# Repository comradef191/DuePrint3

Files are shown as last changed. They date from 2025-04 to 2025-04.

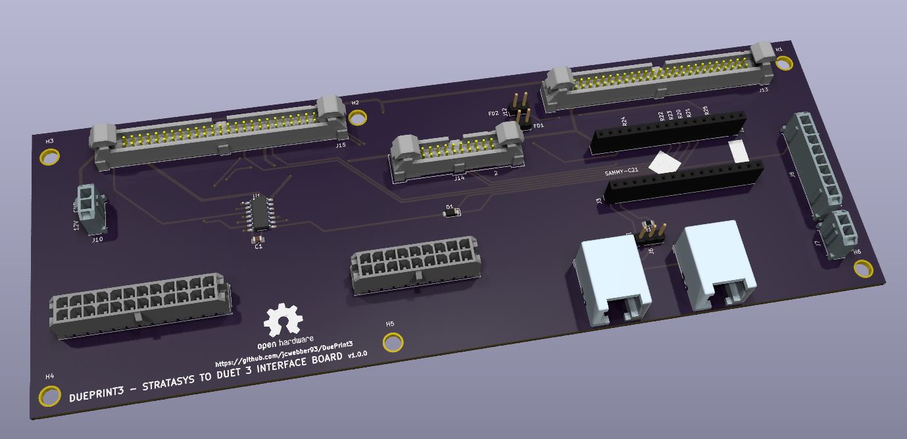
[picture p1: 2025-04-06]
DuePrint3 v1.0.0.JPG

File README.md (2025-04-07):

# DuePrint3
Duet 3 to Stratasys PDB Interface Board. Used to convert a Stratasys Prodigy series printer (Dimension, uPrint, Fortus 250) to use a modern control board & firmware. This conversion is fully reversable (assuming the printer functions to begin with). Many thanks to AJ Quick and Archeantus (Jeremy) for their past efforts in detailing the electronics of the Dimension/uPrint machines, as well as sharing details on their Duet 2 WiFi conversions.
* https://wiki.cnc.xyz/Stratasys_uPrint_Retrofit
* https://forum.duet3d.com/topic/12647/another-stratasys-uprint-retrofit

[Additional details for this project on the Duet3D forums.](https://forum.duet3d.com/topic/37434/dueprint-with-a-duet-3-6hc-stratasys-dimension-conversion)

DuetPrint3 Block Diagram

sIMG_3466

DuePrint3 v1 0 0

At present, the implementation focuses on the Dimension 1200es printers (the implementations linked above focus on the uPrint series, which is quite similar. The electronics are laid out a touch differently, meaning the layout of the new hardware must change, as well where the stepper motor wiring taps in to the existing harness). The Duet 3 Mainboard 6HC, as well as the Sammy-C21 module (natively running RepRapFirmware) interface with 19 inputs, and 9 outputs.
### Inputs
|Input|Description|GCode|Note|
|---|---|---|---|
|6HC IO_7 io7.in|PRINT HEAD TEMP ALARM|`M950 J9 C"!io7.in" ; Print Head Temp Alarm`|Feature not yet implemented|
|6HC IO_2 io2.in|PRINT BED TOUCH PR LIM SW|`M558 P5 H5 F1200:200 T18000 A3 C"!io2.in" ; Z probe`|Used in bed probing|
|6HC IO_6 io6.in|Z-AXIS EOT|`M574 Z2 S1 P"!io6.in"  ; assign Z EOT to x endstop on high side`|Used as part of homing (find max Z)|
|6HC IO_8 io8.in|CHAMBER TEMP ALARM|`M950 J10 C"!io8.in" ; Chamber Temp Alarm`|Feature not yet implemented|
|6HC IO_4 io4.in|Y-AXIS EOT|`M950 J6 C"!io4.in" ; Y-axis EOT`|Used in macro to measure max Y|
|6HC IO_3 io3.in|X-AXIS EOT|`M950 J5 C"!io3.in" ; X-axis EOT`|Used in macro to measure max X|
|6HC IO_0 io0.in|X-AXIS HOME SW|`M574 X1 S1 P"!io0.in" ; X home limit (low side)`|Used in homing|
|6HC IO_1 io1.in|Y-AXIS HOME SW|`M574 Y1 S1 P"!io1.in" ; Y home limit (low side)`|Used in homing|
|6HC IO_5 io5.in|Z-AXIS HOME SW|`M950 J7 C"!io5.in" ; Z-axis Home`|I/O works, Feature not yet implemented|
|SAMMY-C21 PB08|Filament Detection 2|Not Implemented|Feature not yet implemented|
|SAMMY-C21 PA04|Gecko Error|`M950 J0 C"124.pa04" ; Gecko Error In`|Was used to detect an error on Geckodrive G320x. No longer used|
|SAMMY-C21 PA05|HEAD THERMOSTAT STATUS|`M950 J1 C"124.pa05" ;Head Thermostat Status`|Feature not yet implemented|
|SAMMY-C21 PA06|DOOR SWITCH|`M950 J2 C"124.pa06" ; Door`|I/O works, Feature not yet implemented|
|SAMMY-C21 PA07|SUPPORT TOGGLE SW|`M950 J3 C"124.pa07" ; Support Toggle`|Sense Support toolchange|
|SAMMY-C21 PA12|Filament Detection 1|Not Implemented|Feature not yet implemented|
|SAMMY-C21 PA19|MODEL TOGGLE SW|`M950 J4 C"124.pa19" ; Model Toggle`|Sense Model toolchange|
|6HC TEMP_0 VSSA & temp0|CHAMBER THERM|`M308 S0 A"Chamber Test" P"temp0" Y"linear-analog" F0 B-42 C113`||
|6HC TEMP_1 VSSA & temp1|MODEL THERM|`M308 S1 A"Model Test" P"temp1" Y"linear-analog" F0 B12.5 C328`||
|6HC TEMP_2 VSSA & temp2|SUPPORT THERM|`M308 S2 A"Support Test" P"temp2" Y"linear-analog" F0 B12.5 C328`||

### Outputs
|Output|Description|GCode|Note|
|---|---|---|---|
|6HC OUT_8 V_OUTLC8 & out8|EXTRUDER MODEL HEATER ENA|`M950 H1 C"!out8" T1 ; Model, sensor 1`|
|6HC OUT_9 V_OUTLC9 & out9|SUPPORT HEATER ENA|`M950 H2 C"!out9" T2 ; Support, sensor 2`|
|6HC IO_2 io2.out|LED LIGHTS ENA|`M950 P4 C""io2.out"" ; LED Lights - M42 P4 S1 ; lights on`|
|6HC IO_6 io6.out|DOOR SOLENOID ENA|`M950 P3 C""io6.out"" ; Door Solenoid - M42 P3 S0 ; unlocked`|
|6HC OUT_7 V_OUTLC7 & out7|CHAMBER HEATER ENA|`M950 H0 C"!out7" T0 ; Chamber, sensor 0`||
|6HC OUT_6 V_OUTLC6 & out6|PRINT BED TOUCH PR ENA|`M950 P2 C""!out6"" ; Touch Power Enable` - `M42 P2 S0`|Unsure on purpose? Doesn't seem to function at all/as expected|
|6HC IO_0 io0.out|GECKO RESET|`M950 P5 C""io0.out"" ; Gecko Reset` - `M42 P5 S0`|Was used to reset an error on Geckodrive G320x. No longer used|
|6HC OUT_5 V_OUTLC5 & out5|MOTOR ENA|`M950 P1 C""!out5"" ; Extruder Motor` - `M42 P1 S0 ; motor off`|
|6HC OUT_4 V_OUTLC4 & out4|BLOWER ENA|`M950 P0 C""!out4"" ; Head Blower Fan` - `M42 P0 S0 ; enable blower`|

The 6HC directly drives the X, Y, and Z stepper motors (vs. controlling them through the Stratasys PDB). The 6HC, unlike the Duet2 (and Duex boards) does not natively have STEP/DIR pins used to emit step and direction pulses. Instead, a Sammy-C21 ([running RepRapFirmware](https://docs.duet3d.com/Duet3D_hardware/Duet_3_family/Using_the_Sammy-C21_development_board_with_Duet_3)) is used to emit step and direction pulses to a STM32 Nucelo-64, which in turn is running [SimpleDCMotor](https://github.com/simplefoc/Arduino-FOC-dcmotor) to control the extruder's closed loop DC motor. Note that this design was initially setup to use a Geckodrive G320x, however early into commissioning, I burnt up a few series resistors and a 74AC14 on the PDB. The Nucleo-64 with SimpleDCMotor is a much better solution, with a significantly lower cost.

## Materials
[A detailed BOM can be found here](https://github.com/jcwebber93/DuePrint3/blob/main/DuePrint3%20BOM.xlsx), with the approximate cost being ~$500 (60% of this is Duet3D 6HC and Sammy-C21).

## Interface Board Design
[The KidCad project for the DuePrint3 board can be found here](https://github.com/jcwebber93/DuePrint3/tree/main/DuePrint3%20KiCad%20Project)

## Wiring
[A detailed wire list can be found here.](https://github.com/jcwebber93/DuePrint3/blob/main/DuePrint3%20Wire%20List.xlsx) Connectors & crimps for the Duet 3 6HC are supplied with the board, but are JST VH (stepper motors) and Molex KK / Wurth WR-WTB (Wurth connectors/contacts are supplied with Duet Boards). Interface board uses Molex Micro-3.0 series connectors & crimps, whereas the connectors for the PBD ribbon cables are Samtec EHT headers.

> [!WARNING]
> Do not connect connectors `P13`, `P20`, and `P26` (Model heater, support heater, chamber heater) to the 6HC until after the model, support, and chamber thermocouple functionality has been validated

## Sammy-C21 Prep
If using a Sammy-C21 purchased with the preloaded Duet3D bootloader, no special programming is needed. J100 needs to be unbridged, as 5V is supplied to pins 15 and 32 (V33, for 5V logic, and VCC).



## Interface Board Prep
If the Interface Board (w/Sammy-C21) is the only CAN-FD device, aside from the Duet 3 6HC, place a 2-socket jumper here to enable the CAN-FD termination resistor.



J4 connects to the 6HC. J5 (marking suspiciously missing on silkscreen) can be used with additional expansion boards (such as a Duet 3 SZP on the print head, could be used as an accelerometer or for bed scanning), provided the CAN-FD bus is terminated on the additional board.

## RepRapFirmware Prep
At present, the 6HC and Sammy-C21 are running 3.6.0-rc.1 (April 2025). [Configuration files are located here](https://github.com/jcwebber93/DuePrint3/tree/main/Duet%203%20Configuration/System%20Directory), and [Macros are located here.](https://github.com/jcwebber93/DuePrint3/tree/main/Duet%203%20Configuration/Macros%20Directory)

> [!WARNING]
> Do not connect connectors `P13`, `P20`, and `P26` (Model heater, support heater, chamber heater) to the 6HC until after the model, support, and chamber thermocouple functionality has been validated (a spare K-type thermocouple can be used to validate the linear-analog values in the `M308` commands - ice water and boiling water (for the chamber), boiling water for the extruders)

## SimpleDCMotor / Nucleo-64
[Sketch located here](https://github.com/jcwebber93/DuePrint3/tree/main). Prep your build enviornment [per the SimpleFOC documentation.](https://docs.simplefoc.com/) I used Ardiono IDE, and [added boards via](https://github.com/stm32duino/Arduino_Core_STM32/wiki/Getting-Started). I bench programmed the Nucleo-64, then prepped it for install in the Stratasys by janging jumper JP5 to set power via E5V instead of U5V (USB).

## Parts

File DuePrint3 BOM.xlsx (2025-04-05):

 |  |  |  |  | $471.09
Item | Part Number | Description | Quantity | REF | Price | EXT Price | Note | Link
1 |  | Duet 3 Mainboard 6HC | 1 |  | $269.99 | $269.99 |  | https://www.filastruder.com/collections/duet3d/products/duet-3-mainboard-6hc
2 | C45_SC21-D3D | SAMMY-C21 Module | 1 |  | $34.99 | $34.99 | Likely need to source 16pin headers | https://www.filastruder.com/products/sammy-c21-v1-0-duet3d-module
3 | NUCLEO-L476RG | STM32 Nucleo-64, L476RG | 1 |  | $23.99 | $23.99 | Need USB Mini B cable for programming | https://www.amazon.com/dp/B01IO3N646
4 |  | DuePrint3 v1.0.0 PCB | 1 |  | $40.60 | $40.60
5 | LRS-75-48 | Power Suppy, AC/DC, 48V 75W | 1 |  | $15.60 | $15.60 | AC is spliced in from the printer's power inlet, meaning right now the Duet's power cannot be controlled from front on/off switch (though front on/off switch functionality is also not fully present on PCB) | https://www.digikey.com/en/products/detail/mean-well-usa-inc/LRS-75-48/7705054
6 | 430452412 | Conn, Header, 24 pos, Micro-Fit 3.0 | 1 | J1 | $3.51 | $3.51 |  | https://www.digikey.com/en/products/detail/molex/0430452412/531416
7 | 430451812 | Conn, Header, 18 pos, Micro-Fit 3.0 | 1 | J9 | $2.48 | $2.48 |  | https://www.digikey.com/en/products/detail/molex/0430451812/531413
8 | EHT-120-01-S-D | Conn, Header, 40 pos, EHT | 2 | J13,J15 | $13.46 | $26.92 |  | https://www.digikey.com/en/products/detail/samtec-inc/EHT-120-01-S-D/1106698
9 | EHT-110-01-S-D | Conn, Header, 20 pos, EHT | 1 | J14 | $6.54 | $6.54 |  | https://www.digikey.com/en/products/detail/samtec-inc/EHT-110-01-S-D/1106695
10 | PPPC161LFBN-RC | Conn, Header, 16 pos | 2 | J2,J3 | $0.93 | $1.86 |  | https://www.digikey.com/en/products/detail/sullins-connector-solutions/PPPC161LFBN-RC/810188
11 | 54601-906002WPLF | Conn, 6p4c R/A | 2 | J4,J5 | $0.20 | $0.40 |  | https://www.digikey.com/en/products/detail/amphenol-cs-fci/54601-906002WPLF/4242890
12 | 436500215 | Conn, Header, 2 pos, MicroFit- 3.0 | 2 | J7,J10 | $0.89 | $1.78 |  | https://www.digikey.com/en/products/detail/molex/0436500215/283461
13 | M20-9990245 | Conn, Header, 2 pos | 2 | J11,J12 | $0.12 | $0.24 | Can buy larger and cut down | https://www.digikey.com/en/products/detail/harwin-inc/M20-9990245/3728225
14 | M20-9990345 | Conn, Header, 3 pos | 1 | J6 | $0.15 | $0.15 | Can buy larger and cut down | https://www.digikey.com/en/products/detail/harwin-inc/M20-9990345/3728227
15 | 436500815 | Conn, Header, 8 pos, Micro-Fit 3.0 | 1 | J8 | $1.00 | $1.00 |  | https://www.digikey.com/en/products/detail/molex/0436500815/531388
16 | CL21B104KCFSFNE | 0.1 uF Cap, 0805 | 1 | C1 | $0.10 | $0.10 |  | https://www.digikey.com/en/products/detail/samsung-electro-mechanics/cl21b104kcfsfne/3888581
17 | CRCW080531K6FKEA | 31.6K Res, 0805 | 6 | R7,R9,R11,R13,R15,R18 | $0.10 | $0.60 |  | https://www.digikey.com/en/products/detail/vishay-dale/CRCW080531K6FKEA/1175806
18 | CRCW08053K74FKEA | 3740 Res, 0805 | 6 | R8,R10,R12,R14,R16,R19 | $0.10 | $0.60 |  | https://www.digikey.com/en/products/detail/vishay-dale/crcw08053k74fkea/1175701
19 | CRCW080510K0FKEA | 10K Res, 0805 | 6 | R20,R21,R22,R23,R24,R25 | $0.10 | $0.60 |  | https://www.digikey.com/en/products/detail/vishay-dale/crcw080510k0fkea/1175751
20 | CRCW08052K00FKEA | 2K Res, 0805 | 3 | R1,R3,R4 | $0.10 | $0.30 |  | https://www.digikey.com/en/products/detail/vishay-dale/CRCW08052K00FKEA/1175669
21 | CRCW08051K00FKEA | 1K Res, 0805 | 3 | R2,R5,R6 | $0.10 | $0.30 |  | https://www.digikey.com/en/products/detail/vishay-dale/CRCW08051K00FKEA/1175637
22 | CRCW08051K00FKEA | 120 Res, 0805 | 1 | R17 | $0.10 | $0.10 |  | https://www.digikey.com/en/products/detail/vishay-dale/CRCW08051K00FKEA/1175637
23 | SS1FH10-M3/H | Schottky Diode, 100V 1A, DO-219AB | 1 | D1 | $0.32 | $0.32 |  | https://www.digikey.com/en/products/detail/vishay-general-semiconductor-diodes-division/SS1FH10-M3-H/6012246
24 | SN74AHCT125DR | SN74AHCT125DR, 14-SOIC | 1 | U1 | $0.23 | $0.23 |  | https://www.digikey.com/en/products/detail/texas-instruments/SN74AHCT125DR/376412
25 | 39012086 | Conn, Plug, 8 pos, Mini-Fit Jr | 1 | P2 | $0.66 | $0.66 |  | https://www.digikey.com/en/products/detail/molex/0039012086/930285
26 | 39012205 | Conn, Rcpt, 20 pos, Mini-Fit Jr | 1 | P3 | $1.48 | $1.48 |  | https://www.digikey.com/en/products/detail/molex/0039012205/930279
27 | 39012206 | Conn, Plug, 20 pos, Mini-Fit Jr | 1 | P1 | $1.20 | $1.20 |  | https://www.digikey.com/en/products/detail/molex/0039012206/4693014
28 | 39000041 | Pin, 18-24 AWG, Mini-Fit Jr | 10 |  | $0.15 | $1.50 | Don't use these, as they're designed for very large jackets. Recommend 39000049 instead | https://www.digikey.com/en/products/detail/molex/0039000041/61445
29 | 39000039 | Socket, 18-24 AWG, Mini-Fit Jr | 6 |  | $0.16 | $0.96 | Don't use these, as they're designed for very large jackets. Recommend 39000047 instead | https://www.digikey.com/en/products/detail/molex/0039000039/61448
30 | 430300007 | Socket, 20-24 AWG, Micro-Fit 3.0 | 43 |  | $0.18 | $7.74 |  | https://www.digikey.com/en/products/detail/molex/0430300007/252479
31 | 430252400 | Conn, Rcpt, 24 pos, Micro-Fit 3.0 | 1 | P8 | $1.34 | $1.34 |  | https://www.digikey.com/en/products/detail/molex/0430252400/531410
32 | 430251800 | Conn, Rcpt, 18 pos, Micro-Fit 3.0 | 1 | P9 | $1.07 | $1.07 |  | https://www.digikey.com/en/products/detail/molex/0430251800/531407
33 | 436450800 | Conn, Rcpt, 8 pos, Micro-Fit 3.0 | 1 | P10 | $0.35 | $0.35 |  | https://www.digikey.com/en/products/detail/molex/0436450800/531322
34 | VHR-4N | Conn, Rcpt, 4 pos, JST VH | 3 | P4,P5,P6 | $0.12 | $0.36 | Included in 6HC purchase | https://www.digikey.com/en/products/detail/jst-sales-america-inc/VHR-4N/608626
35 | SVH-21T-P1.1 | Socket, 18-22 AWG, JST VH | 12 |  | $0.12 | $1.44 | Included in 6HC purchase | https://www.mouser.com/ProductDetail/JST-Commercial/SVH-21T-P11?qs=QpmGXVUTftHffPDBVqr85w%3D%3D
36 | 61900511621 | Conn, Rcpt, 5 pos, WR-WTB | 9 | P12,P14,P15,P19,P21,P22,P23,P24,P25 | $0.17 | $1.53 | Included in 6HC purchase | https://www.digikey.com/en/products/detail/w%C3%BCrth-elektronik/61900511621/2508639
37 | 61900211621 | Conn, Rcpt, 2 pos, WR-WTB | 6 | P13,P16,P17,P18,P20,P26 | $0.13 | $0.78 | Included in 6HC purchase | https://www.digikey.com/en/products/detail/w%C3%BCrth-elektronik/61900211621/2508636
38 | 61900411621 | Conn, Rcpt, 4 pos, WR-WTB | 3 | P27,P28,P29 | $0.17 | $0.51 | Included in 6HC purchase | https://www.digikey.com/en/products/detail/w%C3%BCrth-elektronik/61900411621/2508638
39 | 61900113722DEC | Socket, 22-28 AWG, WR-WTB | 32 |  | $0.15 | $4.80 | Included in 6HC purchase | https://www.digikey.com/en/products/detail/w%C3%BCrth-elektronik/61900113722DEC/2508640
40 | QPC02SXGN-RC | Jumper, Shorting | 2 |  | $0.10 | $0.20 | For CAN-FD termination, or later filament detector connection | https://www.digikey.com/en/products/detail/sullins-connector-solutions/QPC02SXGN-RC/2618262
41 |  | CAN-FD Cable, 1m | 1 |  | $4.99 | $4.99 |  | https://www.filastruder.com/collections/duet3d/products/duet-can-fd-cable?variant=39510523281479
42 |  | 120pcs 200mm Dupont Jumpers | 1 |  | $6.98 | $6.98 | As required | https://www.amazon.com/dp/B01EV70C78
43 |  | 22 AWG Wire |  |  |  | $0.00 | As required/desired. Smaller gauges likely would be acceptable for most connections excluding motor wires | https://www.remingtonindustries.com/hook-up-wire/hook-up-wire-22-awg-stranded-solid-kit-2-color-sets-2-spool-sizes-available/
44 |  | RJ11 connectors |  |  |  | $0.00 | In case custom length/custom purpose CAN-FD cables are desired

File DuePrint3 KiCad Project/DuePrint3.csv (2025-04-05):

Reference | Value | Datasheet | Footprint | Qty | DNP
C1 | 0.1 µF | https://www.digikey.com/en/products/detail/samsung-electro-mechanics/cl21b104kcfsfne/3888581 | Capacitor_SMD:C_0805_2012Metric_Pad1.18x1.45mm_HandSolder | 1
D1 | 100v 1a | https://www.digikey.com/en/products/detail/vishay-general-semiconductor-diodes-division/SS1FH10-M3-H/6012246 | Diode_SMD:D_SMF | 1
J1 | 430452412 | https://www.digikey.com/en/products/detail/molex/0430452412/531416?s=N4IgTCBcDaICwGYAMcCsBaMcCMEC6AvkA | Connector_Molex:Molex_Micro-Fit_3.0_43045-2412_2x12_P3.00mm_Vertical | 1
J2,J3 | PPPC161LFBN-RC | https://www.digikey.com/en/products/detail/sullins-connector-solutions/PPPC161LFBN-RC/810188 | Connector_PinSocket_2.54mm:PinSocket_1x16_P2.54mm_Vertical | 2
J4,J5 | 6P2C | https://www.digikey.com/en/products/detail/amphenol-cs-fci/54601-906002WPLF/4242890 | Connector_RJ:RJ12_Amphenol_54601-x06_Horizontal | 2
J6 | Conn_01x03_Pin | ~ | Connector_PinHeader_2.54mm:PinHeader_1x03_P2.54mm_Vertical | 1
J7,J10 | 436500215 | https://www.digikey.com/en/products/detail/molex/0436500215/283461?s=N4IgTCBcDaICwGYBsBWADAWjWAjCkAugL5A | Connector_Molex:Molex_Micro-Fit_3.0_43650-0215_1x02_P3.00mm_Vertical | 2
J8 | 436500815 | https://www.digikey.com/en/products/detail/molex/0436500815/531388 | Connector_Molex:Molex_Micro-Fit_3.0_43650-0815_1x08_P3.00mm_Vertical | 1
J9 | 430451812 | https://www.digikey.com/en/products/detail/molex/0430451812/531413 | Connector_Molex:Molex_Micro-Fit_3.0_43045-1812_2x09_P3.00mm_Vertical | 1
J11,J12 | Conn_01x02_Pin | ~ | Connector_PinHeader_2.54mm:PinHeader_1x02_P2.54mm_Vertical | 2
J13,J15 | EHT-125-01-S-D | https://www.digikey.com/en/products/detail/samtec-inc/EHT-120-01-S-D/1106698 | EHT-125-01-S-D:SAMTEC_EHT-125-01-S-D | 2
J14 | EHT-110-01-S-D | https://www.digikey.com/en/products/detail/samtec-inc/EHT-110-01-S-D/1106695 | EHT-110-01-XX-D:EHT-110-01-XX-D | 1
R1,R3,R4 | 2K | https://www.digikey.com/en/products/detail/vishay-dale/CRCW08052K00FKEA/1175669 | Resistor_SMD:R_0805_2012Metric_Pad1.20x1.40mm_HandSolder | 3
R2,R5,R6 | 1K | https://www.digikey.com/en/products/detail/vishay-dale/CRCW08051K00FKEA/1175637 | Resistor_SMD:R_0805_2012Metric_Pad1.20x1.40mm_HandSolder | 3
R7,R9,R11,R13,R15,R18 | 31.6K | https://www.digikey.com/en/products/detail/vishay-dale/CRCW080531K6FKEA/1175806 | Resistor_SMD:R_0805_2012Metric_Pad1.20x1.40mm_HandSolder | 6
R8,R10,R12,R14,R16,R19 | 3740 | https://www.digikey.com/en/products/detail/vishay-dale/crcw08053k74fkea/1175701 | Resistor_SMD:R_0805_2012Metric_Pad1.20x1.40mm_HandSolder | 6
R17 | 120 | https://www.digikey.com/en/products/detail/vishay-dale/CRCW08051K00FKEA/1175637 | Resistor_SMD:R_0805_2012Metric_Pad1.20x1.40mm_HandSolder | 1
R20,R21,R22,R23,R24,R25 | 10k | https://www.digikey.com/en/products/detail/vishay-dale/crcw080510k0fkea/1175751 | Resistor_SMD:R_0805_2012Metric_Pad1.20x1.40mm_HandSolder | 6
U1 | SN74AHCT125DR | https://www.digikey.com/en/products/detail/texas-instruments/SN74AHCT125DR/376412 | Stratasys Adapter:SOIC127P600X175-14N | 1

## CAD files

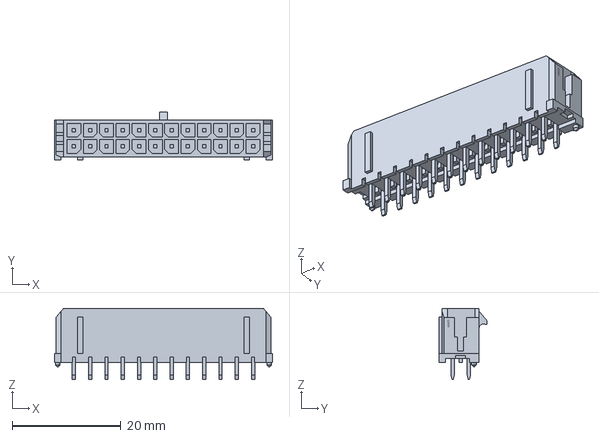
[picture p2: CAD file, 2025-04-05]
DuePrint3 KiCad Project/Components/MF3-2x12-430452427.stp
40.1 x 8.77 x 13.1 mm

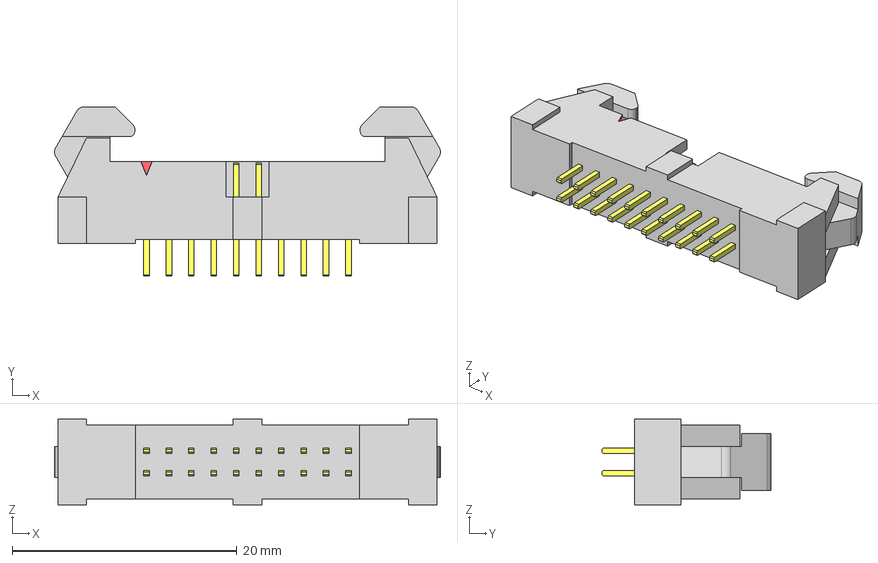
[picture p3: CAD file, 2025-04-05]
DuePrint3 KiCad Project/Components/EHT-110-01-XX-D.step
34.4 x 15.1 x 7.62 mm
C-95-01-10-D-
EHT-First_Position_Indicator
EHT-110-01-D_header

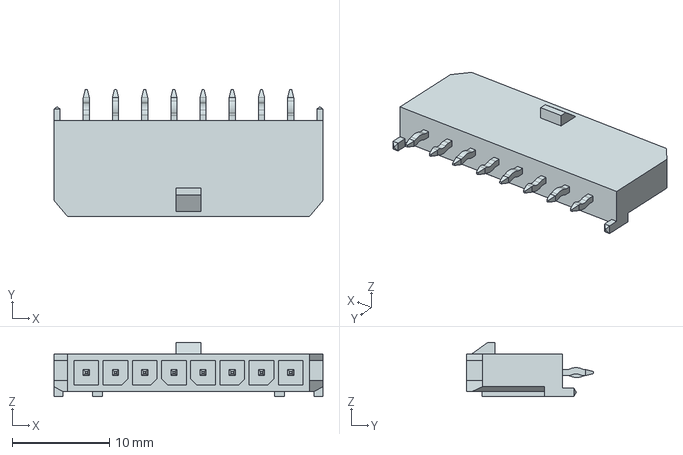
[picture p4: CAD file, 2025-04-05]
DuePrint3 KiCad Project/Components/MF3-1x8-436500815.stp
27.6 x 13.1 x 5.57 mm

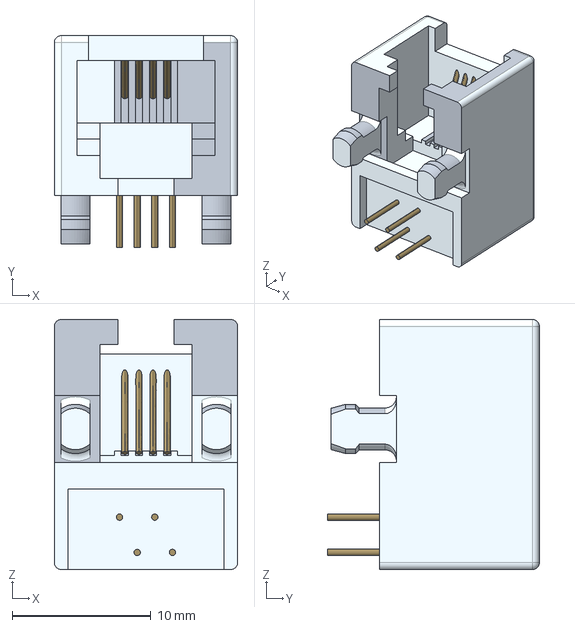
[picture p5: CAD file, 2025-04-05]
DuePrint3 KiCad Project/Components/RJ11-54601.igs
13.2 x 15.2 x 18.0 mm

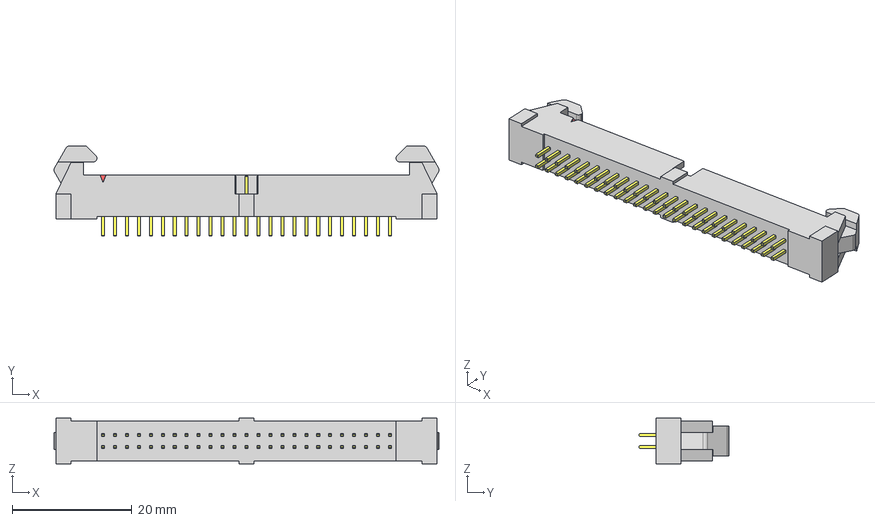
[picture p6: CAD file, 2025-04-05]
DuePrint3 KiCad Project/Components/EHT-125-01-S-D.step
64.4 x 15.1 x 7.62 mm
C-95-01-25-D-
EHT-First_Position_Indicator
EHT-125-01-D_header

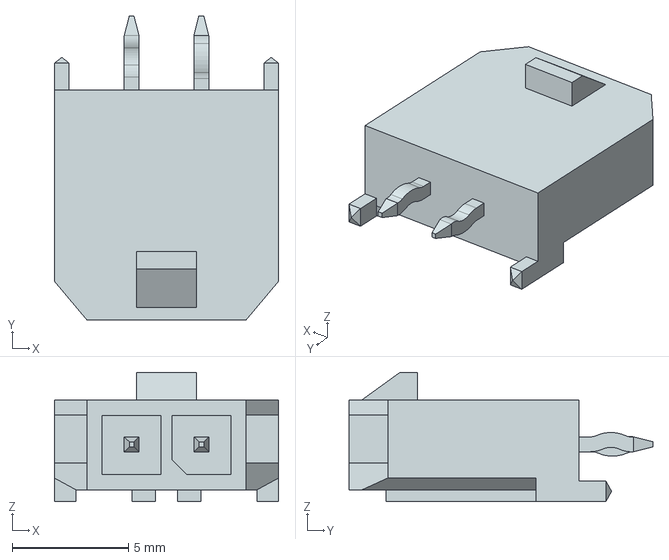
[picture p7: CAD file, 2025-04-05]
DuePrint3 KiCad Project/Components/MF3-1x2-436500215.stp
9.65 x 13.1 x 5.57 mm

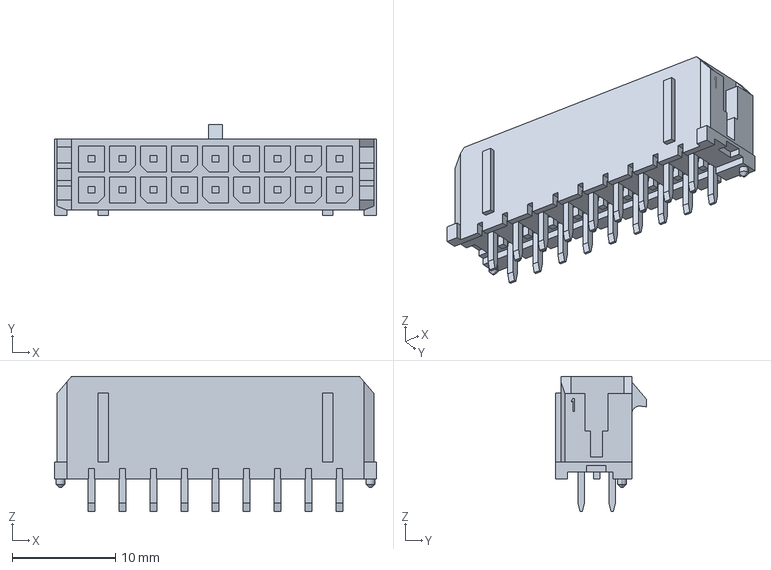
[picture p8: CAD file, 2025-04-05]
DuePrint3 KiCad Project/Components/MF3-2x9-430451827.step
31.1 x 8.77 x 13.1 mm

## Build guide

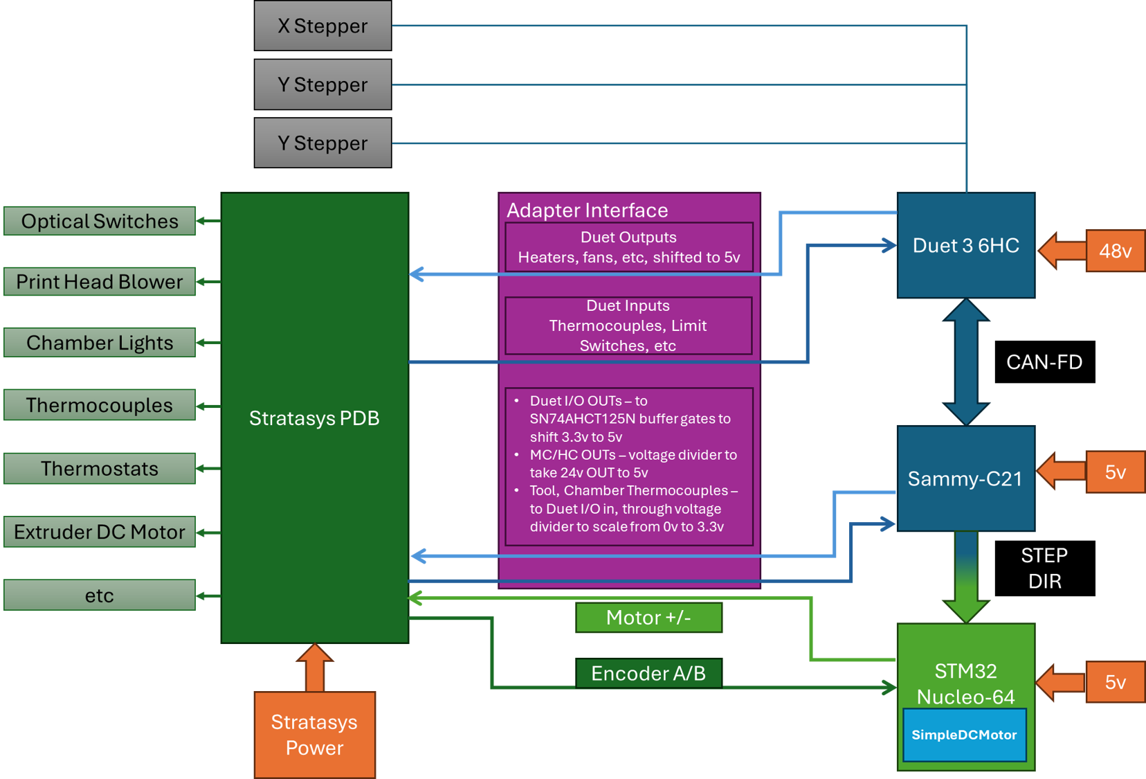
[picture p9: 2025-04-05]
DuetPrint3 Block Diagram.png

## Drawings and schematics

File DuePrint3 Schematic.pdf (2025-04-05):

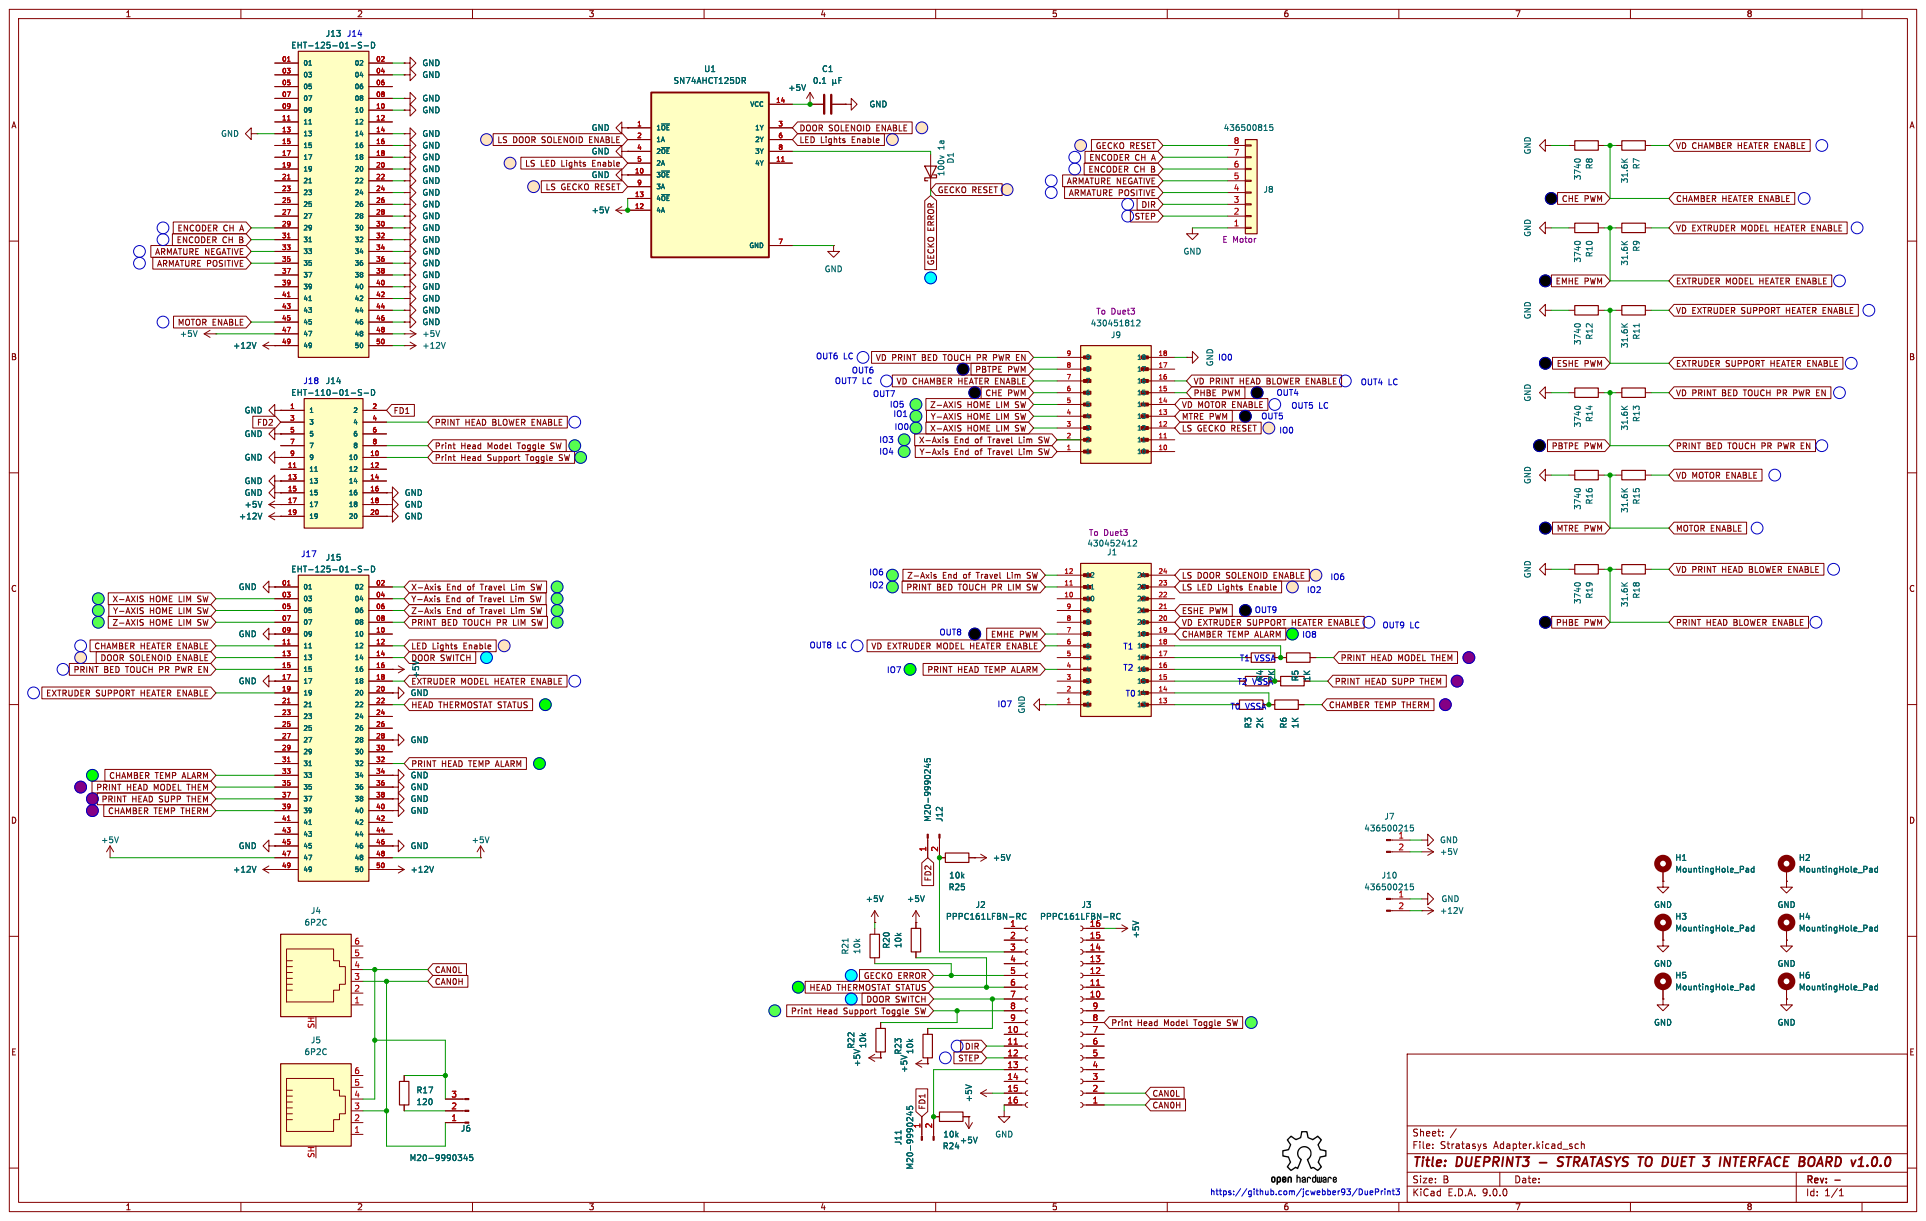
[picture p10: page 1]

LS DOOR SOLENOID ENABLE

ARMATURE NEGATIVE GECKO RESET ARMATURE POSITIVE
ENCODER CH A
ENCODER CH B

VD CHAMBER HEATER ENABLE

LS LED Lights Enable

GND GND

VD EXTRUDER MODEL HEATER ENABLE

EXTRUDER MODEL HEATER ENABLE

VD EXTRUDER SUPPORT HEATER ENABLE

VD PRINT BED TOUCH PR PWR EN

EXTRUDER SUPPORT HEATER ENABLE

VD PRINT HEAD BLOWER ENABLE

Z-AXIS HOME LIM SW
Y-AXIS HOME LIM SW
X-AXIS HOME LIM SW

PRINT HEAD BLOWER ENABLE

Print Head Model Toggle SW
Print Head Support Toggle SW

Y-Axis End of Travel Lim SW

PRINT BED TOUCH PR PWR EN

PRINT HEAD BLOWER ENABLE MOTOR ENABLE

+12V GND GND GND GND GND GND

LS DOOR SOLENOID ENABLE CAN0H
PRINT BED TOUCH PR LIM SW

CHAMBER HEATER ENABLE
DOOR SOLENOID ENABLE

EXTRUDER MODEL HEATER ENABLE DOOR SWITCH
H1 MountingHole_Pad +5V GND

PRINT HEAD MODEL THEM

PRINT HEAD TEMP ALARM

PRINT HEAD SUPP THEM

+5V GND GND GND GND GND GND

CAN0L PRINT HEAD TEMP ALARM

CHAMBER TEMP ALARM
CHAMBER TEMP THERM

Id: 1/1 Title: DUEPRINT3 - STRATASYS TO DUET 3 INTERFACE BOARD v1.0.0

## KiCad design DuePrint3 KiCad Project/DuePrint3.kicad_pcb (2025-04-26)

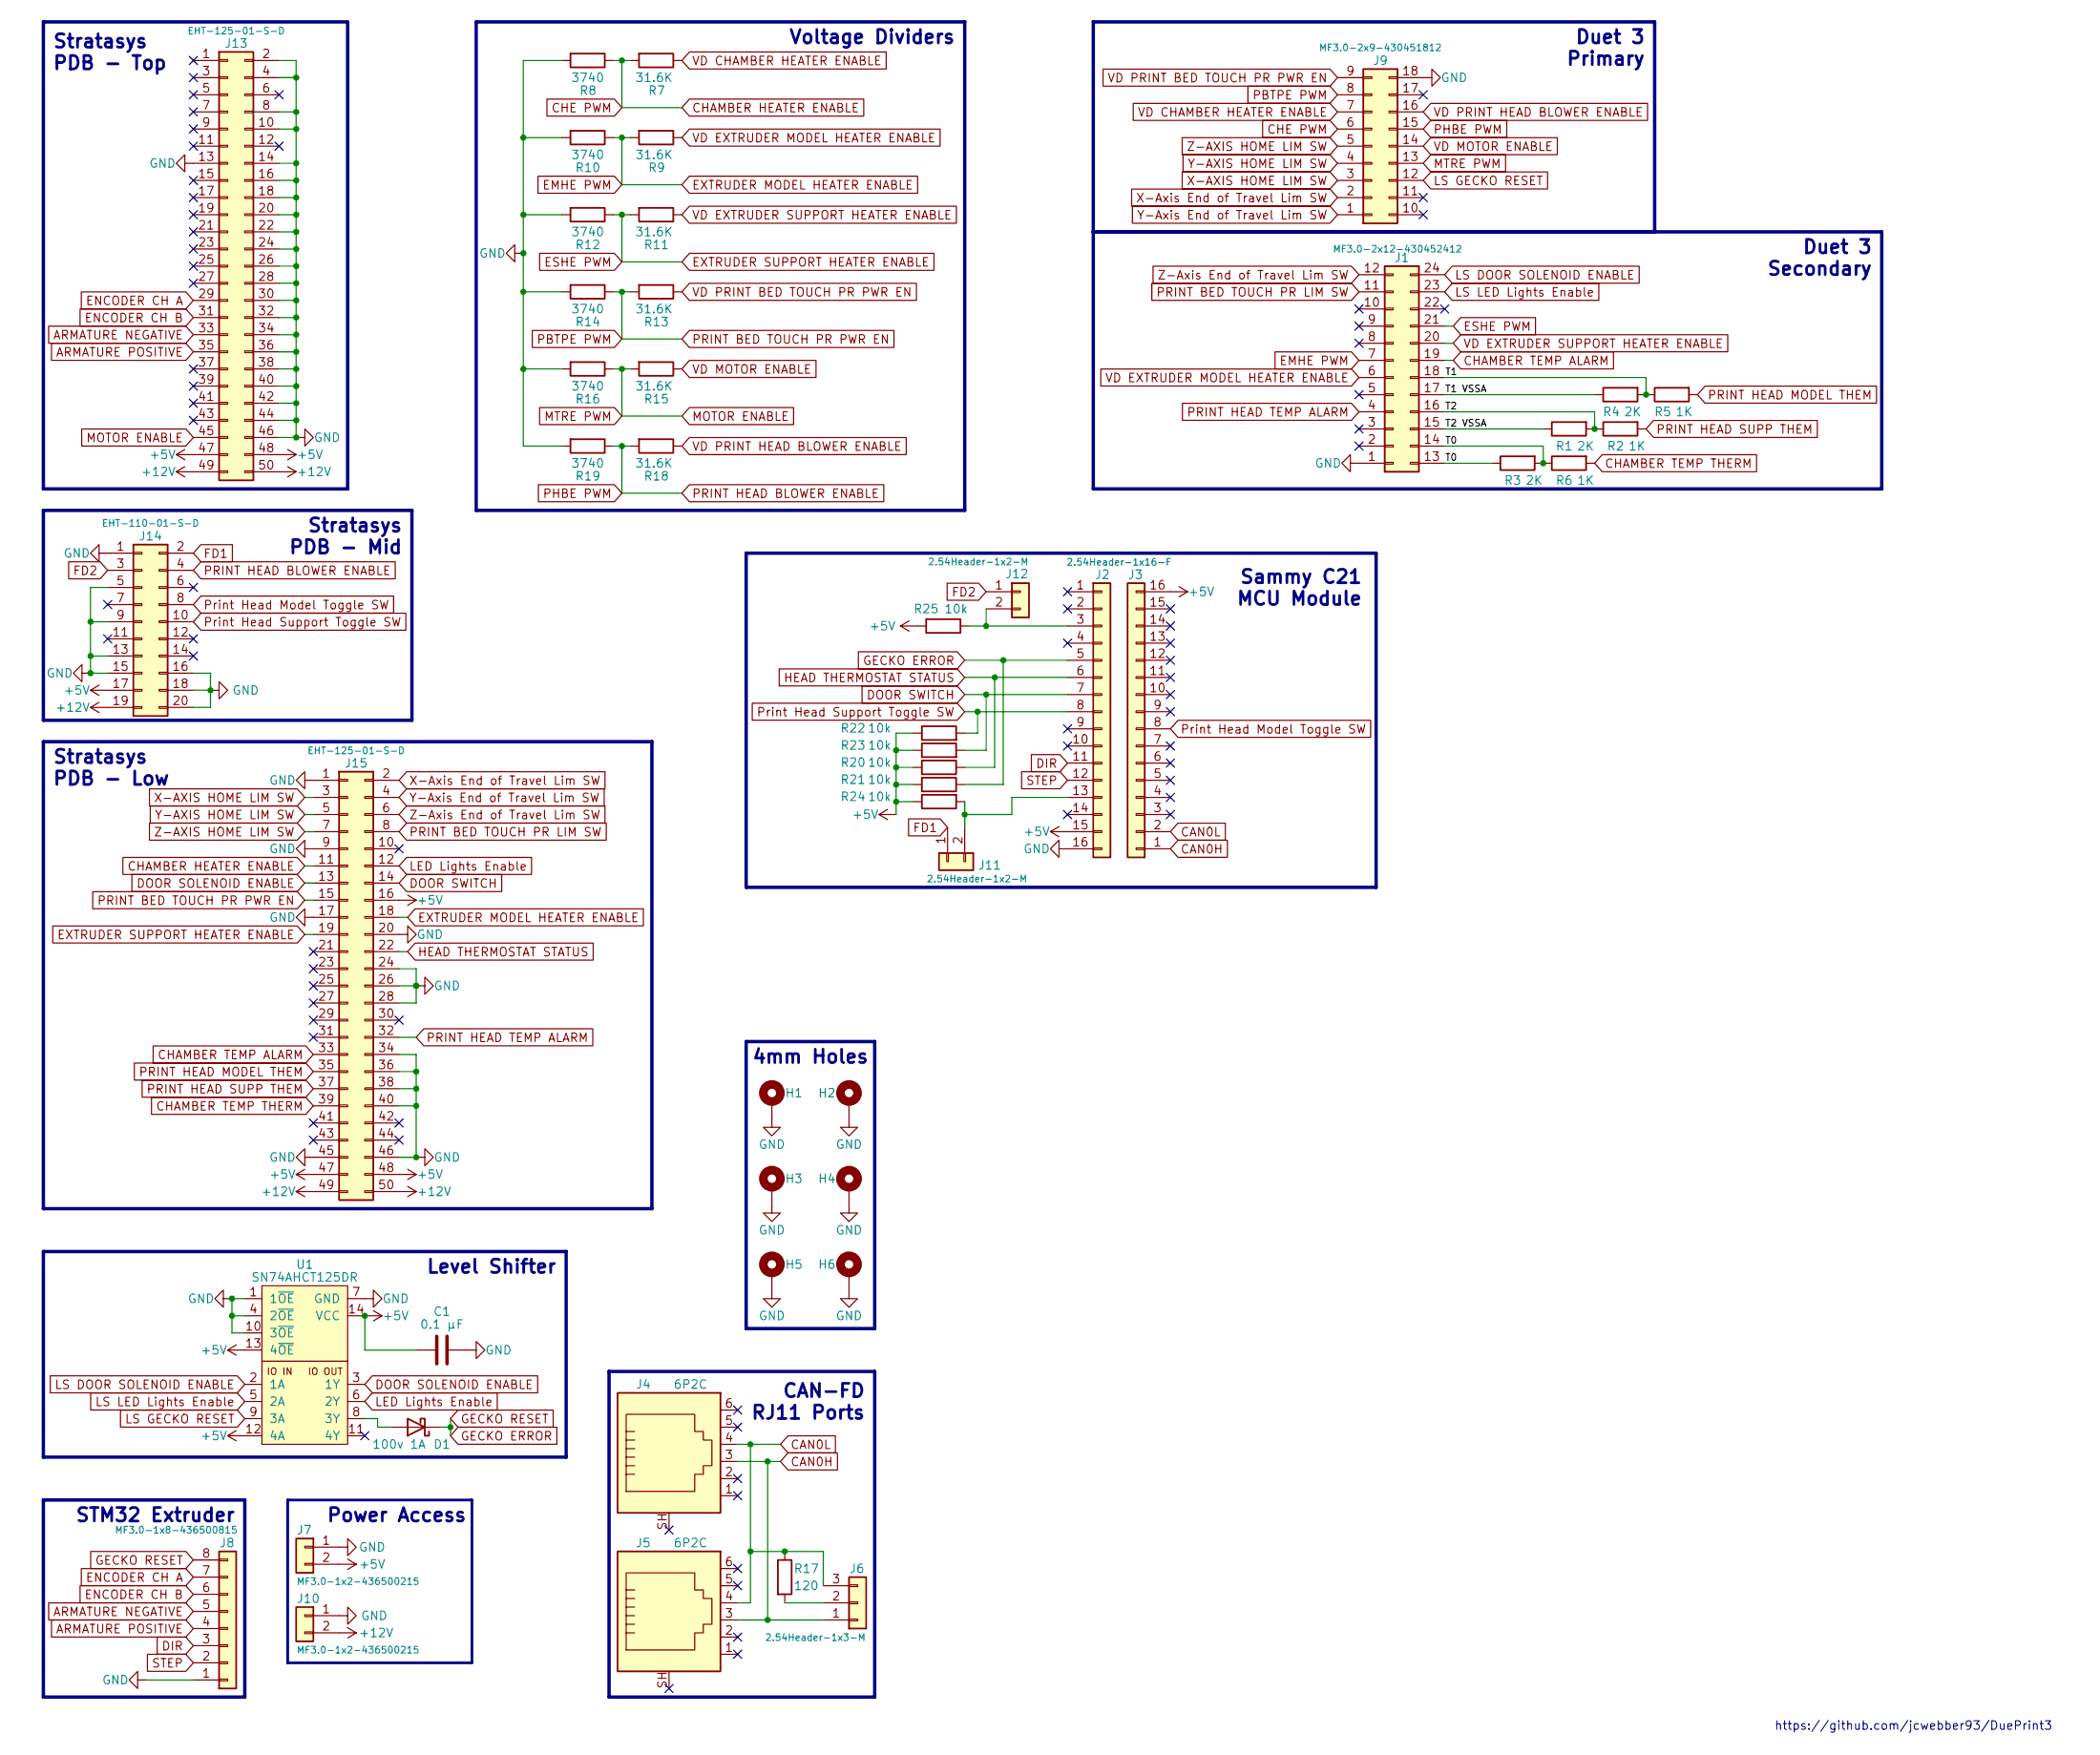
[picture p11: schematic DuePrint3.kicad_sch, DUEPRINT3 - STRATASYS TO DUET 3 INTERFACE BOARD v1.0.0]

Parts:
C1: 0.1 µF; C_0805_2012Metric_Pad1.18x1.45mm_HandSolder
D1: 100v 1A; D_SMF
H1, H2, H3, H4, H5, H6: MountingHole_Pad; MountingHole_4.00mm_Pad
J1: MF3.0-2x12-430452412; Molex_Micro-Fit_3.0_43045-2412_2x12_P3.00mm_Vertical
J2, J3: 2.54Header-1x16-F; PinSocket_1x16_P2.54mm_Vertical
J4, J5: 6P2C; RJ12_Amphenol_54601-x06_Horizontal
J6: 2.54Header-1x3-M; PinHeader_1x03_P2.54mm_Vertical
J7, J10: MF3.0-1x2-436500215; Molex_Micro-Fit_3.0_43650-0215_1x02_P3.00mm_Vertical
J8: MF3.0-1x8-436500815; Molex_Micro-Fit_3.0_43650-0815_1x08_P3.00mm_Vertical
J9: MF3.0-2x9-430451812; Molex_Micro-Fit_3.0_43045-1812_2x09_P3.00mm_Vertical
J11, J12: 2.54Header-1x2-M; PinHeader_1x02_P2.54mm_Vertical
J13, J15: EHT-125-01-S-D; SAMTEC_EHT-125-01-S-D
J14: EHT-110-01-S-D; EHT-110-01-XX-D
R1, R3, R4: 2K; R_0805_2012Metric_Pad1.20x1.40mm_HandSolder
R2, R5, R6: 1K; R_0805_2012Metric_Pad1.20x1.40mm_HandSolder
R7, R9, R11, R13, R15, R18: 31.6K; R_0805_2012Metric_Pad1.20x1.40mm_HandSolder
R8, R10, R12, R14, R16, R19: 3740; R_0805_2012Metric_Pad1.20x1.40mm_HandSolder
R17: 120; R_0805_2012Metric_Pad1.20x1.40mm_HandSolder
R20, R21, R22, R23, R24, R25: 10k; R_0805_2012Metric_Pad1.20x1.40mm_HandSolder
U1: SN74AHCT125DR; SOIC-14_3.9x8.7mm_P1.27mm

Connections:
+5V: C1.1, J2.15, J3.16, J7.2, J13.47, J13.48, J14.17, J15.16, J15.47, J15.48, R20.2, R21.2, R22.1, R23.1, R24.1, R25.1, U1.12 (4A), U1.13 (4~OE), U1.14 (VCC)
+12V: J10.2, J13.49, J13.50, J14.19, J15.49, J15.50
/T0: J1.13, J1.14, R3.1, R3.2, R6.1
/T1: J1.18, R4.2, R5.1
/T1 VSSA: J1.17, R4.1
/T2: J1.16, R1.2, R2.1
/T2 VSSA: J1.15, R1.1
ARMATURE NEGATIVE: J8.5, J13.33
ARMATURE POSITIVE: J8.4, J13.35
CAN0H: J3.1, J4.3, J5.3, J6.1
CAN0L: J3.2, J4.4, J5.4, J6.3, R17.1
CHAMBER HEATER ENABLE: J9.6, J15.11, R7.2, R8.1
CHAMBER TEMP ALARM: J1.19, J15.33
CHAMBER TEMP THERM: J15.39, R6.2
DIR: J2.11, J8.3
DOOR SOLENOID ENABLE: J15.13, U1.3 (1Y)
DOOR SWITCH: J2.7, J15.14, R23.2
EMHE PWM: J1.7, J15.18, R9.2, R10.1
ENCODER CH A: J8.7, J13.29
ENCODER CH B: J8.6, J13.31
ESHE PWM: J1.21, J15.19, R11.2, R12.1
FD1: J11.1, J14.2
FD2: J12.1, J14.3
GECKO ERROR: D1.1 (K), J2.5, J8.8, R21.1
GND: C1.2, H1.1, H2.1, H3.1, H4.1, H5.1, H6.1, J1.1, J2.16, J7.1, J8.1, J9.18, J10.1, J13.2, J13.4, J13.8, J13.10, J13.13, J13.14, J13.16, J13.18, J13.20, J13.22, J13.24, J13.26, J13.28, J13.30, J13.32, J13.34, J13.36, J13.38, J13.40, J13.42, J13.44, J13.46, J14.1, J14.5, J14.9, J14.13, J14.15, J14.16, J14.18, J14.20, J15.1, J15.9, J15.17, J15.20, J15.24, J15.26, J15.28, J15.34, J15.36, J15.38, J15.40, J15.45, J15.46, R8.2, R10.2, R12.2, R14.2, R16.2, R19.2, U1.1 (1~OE), U1.4 (2~OE), U1.7 (GND), U1.10 (3~OE)
HEAD THERMOSTAT STATUS: J2.6, J15.22, R20.1
LED Lights Enable: J15.12, U1.6 (2Y)
LS DOOR SOLENOID ENABLE: J1.24, U1.2 (1A)
LS GECKO RESET: J9.12, U1.9 (3A)
LS LED Lights Enable: J1.23, U1.5 (2A)
MOTOR ENABLE: J9.13, J13.45, R15.2, R16.1
unnamed: D1.2 (A), U1.8 (3Y)
unnamed: J6.2, R17.2
unnamed: J2.13, J11.2, R24.2
unnamed: J2.3, J12.2, R25.2
PBTPE PWM: J9.8, J15.15, R13.2, R14.1
PHBE PWM: J9.15, J14.4, R18.2, R19.1
PRINT BED TOUCH PR LIM SW: J1.11, J15.8
PRINT HEAD MODEL THEM: J15.35, R5.2
PRINT HEAD SUPP THEM: J15.37, R2.2
PRINT HEAD TEMP ALARM: J1.4, J15.32
Print Head Model Toggle SW: J3.8, J14.8
Print Head Support Toggle SW: J2.8, J14.10, R22.2
STEP: J2.12, J8.2
VD CHAMBER HEATER ENABLE: J9.7, R7.1
VD EXTRUDER MODEL HEATER ENABLE: J1.6, R9.1
VD EXTRUDER SUPPORT HEATER ENABLE: J1.20, R11.1
VD MOTOR ENABLE: J9.14, R15.1
VD PRINT BED TOUCH PR PWR EN: J9.9, R13.1
VD PRINT HEAD BLOWER ENABLE: J9.16, R18.1
X-AXIS HOME LIM SW: J9.3, J15.3
X-Axis End of Travel Lim SW: J9.2, J15.2
Y-AXIS HOME LIM SW: J9.4, J15.5
Y-Axis End of Travel Lim SW: J9.1, J15.4
Z-AXIS HOME LIM SW: J9.5, J15.7
Z-Axis End of Travel Lim SW: J1.12, J15.6

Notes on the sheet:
Duet 3 Secondary
STM32 Extruder
4mm Holes
Stratasys PDB - Mid
Sammy C21 MCU Module
CAN-FD RJ11 Ports
Stratasys PDB - Low
Stratasys PDB - Top
https://github.com/jcwebber93/DuePrint3
Duet 3 Primary
Level Shifter
Voltage Dividers
Power Access

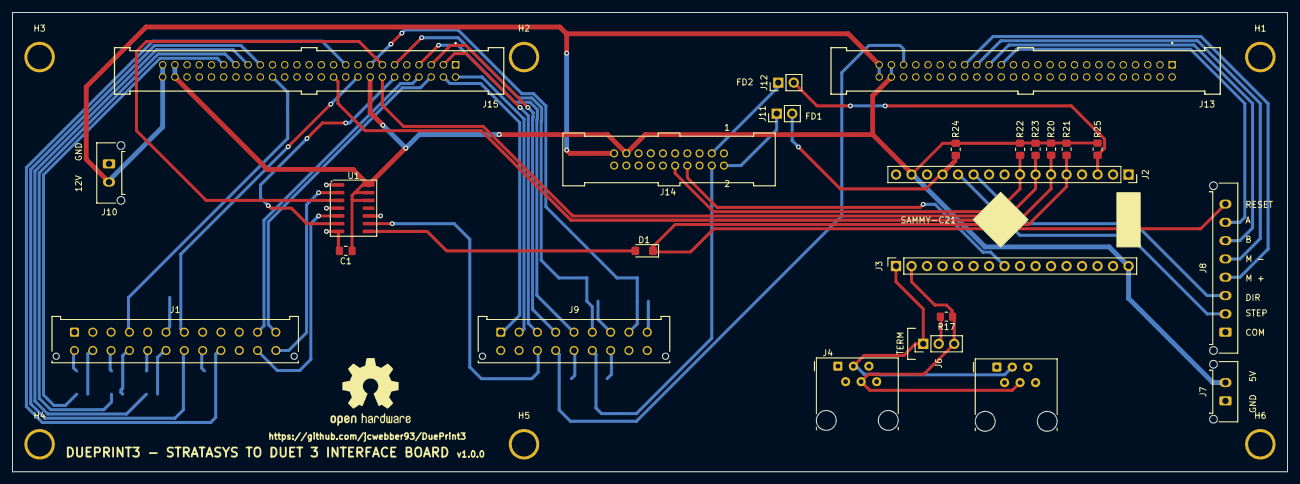
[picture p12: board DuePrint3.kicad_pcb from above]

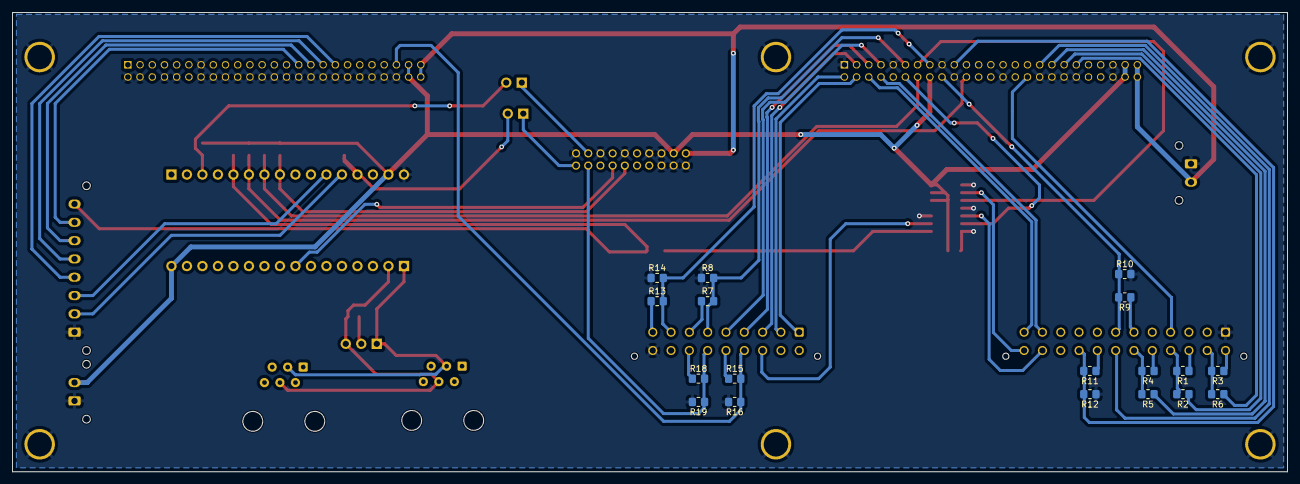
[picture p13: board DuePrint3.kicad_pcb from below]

Board: 2 copper layers, 208.9 x 75.2 mm, 49 parts (18 on the bottom side), 56 nets.

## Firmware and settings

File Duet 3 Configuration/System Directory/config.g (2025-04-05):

; Default config.g template for DuetPi
; Replace this with a proper configuration file (e.g from https://configtool.reprapfirmware.org)

; Display initial welcome message
;M291 P"Please go to <a href=""https://www.duet3d.com/StartHere"" target=""_blank"">this</a> page for further instructions on how to set it up." R"Welcome to your new Duet 3!" S1 T0

; Enable network
if {network.interfaces[0].type = "ethernet"}
    M552 P192.168.100.56 S1
else
    M552 I1 S1

M552 I1 S1                            ; enable wifi

G4 S5                                 ;wait for expansion boards to start

; Drives
M569 P0 S1                            ;physical drive 0 goes backwards, X-Axis
M569 P1 S0                            ;physical drive 1 goes forwards, Y-Axis
M569 P2 S1                            ;physical drive 2 goes forwards, Z-Axis
M569 P124.0 S0 T0:0:0:0               ;external driver on sammy
M584 X0 Y1 Z2 E124.0                  ;set drive mapping
M350 X16 Y16 Z16 E16 I1               ;configure microstepping with interpolation
M92 X53.33 Y134 Z629.864 E3230.77     ;set steps per mm was 1011.99 then 1594.6, then 642.61 
M566 X600 Y600 Z60 E3000              ;set jerk
M203 X30000 Y18000 Z1200 E1800.00      ;set max speeds (mm/min)
M201 X2500 Y3500 Z2000 E3000            ;set max accelerations (mm/s^2)
M201.1 X750 Y750 Z2000 E3000            ;max special acceleration move (homing)
M906 X1800 Y2600 Z2600 I30            ;set motor currents (mA) and motor idle percent
M84 S30                               ;set idle timeout

M208 X-138.3 Y-137.5 Z-2 S1           ;set axis minima
M208 X160.4 Y178.5 Z325.2 S0              ;set axis maxima
; Toggle nozzle min - -163.2 , 206 max
; X EOT toggles at 181.2
; Y EOT at 182.4
;purge bucket near middle - x162.5, y155.5

;z probe left toggle -136.5
;z probe right toggle 197.5

;from build plate center, model (right) offset x=+20.8 (too far right), support is +40.8
;from build plate center, Y offset = -23 (too far forward)

;Z bottom (EOT) 325.1



;Endstops

M574 X1 S1 P"!io0.in"                 ; X home limit (low side)
M574 Y1 S1 P"!io1.in"                 ; Y home limit (low side, toward front of printer
M574 Z2 S1 P"!io6.in"                   ; assign Z EOT to x endstop on high side


; Z-Probe
M558 P5 H5 F1200:200 T18000 A3 C"!io2.in" ; Z probe, set dive height, probe speed and travel speed
;G31 P1000 X-46 Y-74 Z0.896
;G31 P1000 X-24 Y-73 Z1.365
G31 P1000 X24 Y73 Z1.9                    ;Increase value to bring it closer to the bed, decrease to move it away
;G31 P1000 X24 Y96 Z0.896                          ; set Z probe trigger value, offset and trigger height
;M557 X-135:135 Y-135:65 P5:5          ; define mesh grid. The whole bead cannot be probed due to the position of the probe.
M557 X-134:140 Y-127:146.82 P2:2          ; define mesh grid. The whole bead cannot be probed due to the position of the probe.

; Head Blower Fan
M950 P0 C"!out4"
M42 P0 S0                             ; enable blower

; Extruder Motor Enable
M950 P1 C"!out5"
M42 P1 S0

; Touch Power Enable
M950 P2 C"!out6"
M42 P2 S0

; Door Enable
M950 P3 C"io6.out"
M42 P3 S0

; LED Lights Enable
M950 P4 C"io2.out"
M42 P4 S1                             ;S1 to turn on!

; Gecko Reset
M950 P5 C"io0.out"
M42 P5 S0

; Thermocouples
M308 S0 A"Chamber Test" P"temp0" Y"linear-analog" F0 B-42 C113
M308 S1 A"Model Test" P"temp1" Y"linear-analog" F0 B12.5 C328
M308 S2 A"Support Test" P"temp2" Y"linear-analog" F0 B12.5 C328

; Heaters
M140 H-1                              ;Disable bed heater
M950 H0 C"!out7" T0                   ; chamber, sensor 0
M141 H0                               ; map chamber to heater 0
M143 H0 S85                           ; set temperature limit for heater 0 to 85C
M570 H0 P60 T10                       ; Increase fault delay to 30s, decrease temperature fault to 10c
M950 H1 C"!out8" T1                   ; model, sensor 1
M143 H1 S320
M570 H1 P30                           ; set fault time delay to 30s for heater 1
M950 H2 C"!out9" T2                   ; support, sensor 2
M143 H2 S320                          ; set temperature limit for heater 1 to 320C
M570 H2 P30                           ; set fault time delay to 30s for heater 2
; Tools
M563 P0 S"Model" D0 H1                ; define tool 0
G10 P0 X0 Y0 Z0                       ; set tool 0 axis offsets
G10 P0 R0 S0                          ; set initial tool 0 active and standby temperatures

M563 P1 S"Support" D0 H2              ; define tool 1
G10 P1 X-20 Y0 Z-0.1                     ; set tool 1 axis offsets
G10 P1 R0 S0                          ; set initial tool 1 active and standby temperatures



; Gecko Error In
M950 J0 C"124.pa04"                   ;gecko error in

; Head Thermostat Status
M950 J1 C"124.pa05"

; Door In
M950 J2 C"124.pa06"

; Print Head Support Toggle
M950 J3 C"124.pa07"

; Print Head Model Toggle
M950 J4 C"124.pa19"

; X-axis EOT
M950 J5 C"!io3.in"

; Y-axis EOT
M950 J6 C"!io4.in"

; Z-axis Home
M950 J7 C"!io5.in"

; Z-axis EOT
;M950 J8 C"!io6.in"

; Print Head Temp Alarm
M950 J9 C"!io7.in"

; Chamber Temp Alarm
M950 J10 C"!io8.in"


;M581 Tx P5:6:7:8

M955 P120.0 I01
M501                                  ;config g
M302 S280 R280
M572 D0 S.061
M593 P"zvdd" F43
M207 P0 S0.3 F1800
M207 P1 S0.3 F1800
M98 P"globals.g"

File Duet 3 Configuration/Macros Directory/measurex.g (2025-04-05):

M950 J5 C"nil"  ; X-axis EOT unassign
M574 X2 S1 P"!io3.in"  ; assign X EOT to x endstop on high side
G1 H4 X165 F1200
M574 X1 S1 P"!io0.in" ;reassign old x home
M950 J5 C"!io3.in"      ; X-axis EOT

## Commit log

2025-04-05 Initial Release
    KiCad Project, wire list
    [430451827.step, 430452427.stp, 436500215.stp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]
2025-04-05 Updated Wire List, BOM
    [430451827.step, 430452427.stp, 436500215.stp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]
2025-04-05 Add Duet 3 configuration files
    [ProbeAvgZ.g, Wipe.g, config-override.g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]
2025-04-06 File updates
    [DuePrint3 Wire List.xlsx, DuePrint3.kicad_sch]
2025-04-26 Reformat Duet3 connectors
    [DuePrint3.kicad_sch]
2025-04-26 Voltage Dividers
    [DuePrint3.kicad_sch]
2025-04-26 Level shifter
    [DuePrint3.kicad_sch]
2025-04-26 PDB Connectors
    [DuePrint3.kicad_sch]
2025-04-26 The Rest Of The Schematic
    [DuePrint3.kicad_sch]
2025-04-26 also kicad gitignore pls
2025-04-26 Footprint & Symbol reorg; PCB & Schematic now cleaned-up
    [430451827.step, 430452427.stp, 436500215.stp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]

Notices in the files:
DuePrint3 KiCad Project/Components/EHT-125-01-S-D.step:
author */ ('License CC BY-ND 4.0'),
